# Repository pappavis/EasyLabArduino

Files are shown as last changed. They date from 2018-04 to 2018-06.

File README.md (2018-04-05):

### EasyLab Arduino Robotauto
Arduino Robot alles-op-één bordje door **Michiel Erasmus** / EasyLab4Kids. Dit is die tegniese ontwerpe daarvan.<br/>

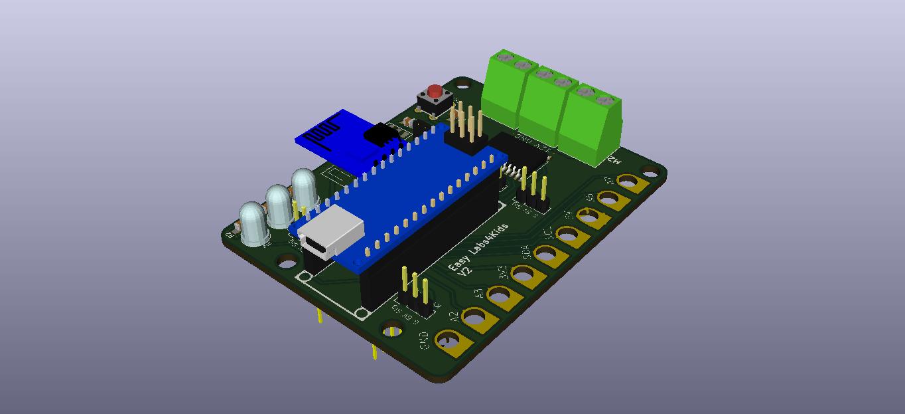
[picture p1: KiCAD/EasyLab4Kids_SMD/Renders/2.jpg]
<br/>

Credits:
---
**Ontwerp** deur Michiel Erasmus<br/>
**Kontak** thebapodcast@gmail.com<br/>
**Voorbeelde** https://www.facebook.com/EasyBlocks4Kids/<br/>
<br/>

EasyLab basis
---
Wat maak die EasyLab so besonder?<br/>
 - Robotauto op die planeet **MARS!!**
 - Volledig praktyk getest op kinders in Nederland<br/>
 - Beskikbaar met online lesmateriaal in Zuid-Afrikaans en Nederlands<br/>
 
EasyLab tegniese moontlikhede
---
Vir mense met 'n computer brein..<br/>
 - Support vir 2x robotmotors<br/>
 - 1x servo aansluiting<br/>
 - 2x Lynvolg snesore aansluitinge
 - 7x koperplaat aansluiting om maklik 'goedkope' aliexpress-sensore te kan gebruik<br/>
 - Skroefverbindinge vir robotmotors<br/>
 - GPIO en IO-poorte is almal beskikbaar
 - Beskikbaar in twee smake: Arduino en Raspberry Pi<br/>
 <br/>
 Elke EasyLab wordt ambagtelik in Den Haag, Nederland gemaak deur personeel met 'n mentaal of fysieke beperking. Dit help mee aan 'n menswaardig bestaan.<br/>

Self probeer?
---
kyk dan op https://www.facebook.com/EasyBlocks4Kids/ <br/>
<br/>
**EasyLab4Kids met LCD skerm en afstandmeting sensor;**<br/>
<br/>
<br/>
**EasyLab nuusgierige by CoderDojo Den Haag, Nederland [Jun-2017]**<br/>
<br/>
<br/>
Wil jy ook 'n EasyLab? Kontak thebapodcast@gmail.com<br/>
<br/>
<br/>
#easylab4kids #easyblocks4kids #arduinorobot
<br/>

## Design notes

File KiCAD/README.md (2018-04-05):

Arduino robot aansturing en breakout bordje<br/>
Ontwerp: Michiel Erasmus<br/>
<br/><br/>
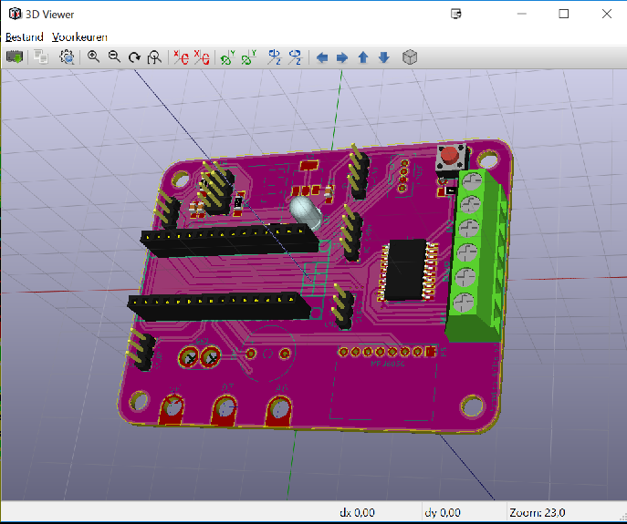
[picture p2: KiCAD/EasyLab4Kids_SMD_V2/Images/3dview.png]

<br/>

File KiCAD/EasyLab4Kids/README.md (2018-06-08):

###EasyLab Arduino V1.0
Arduino Nano versie.

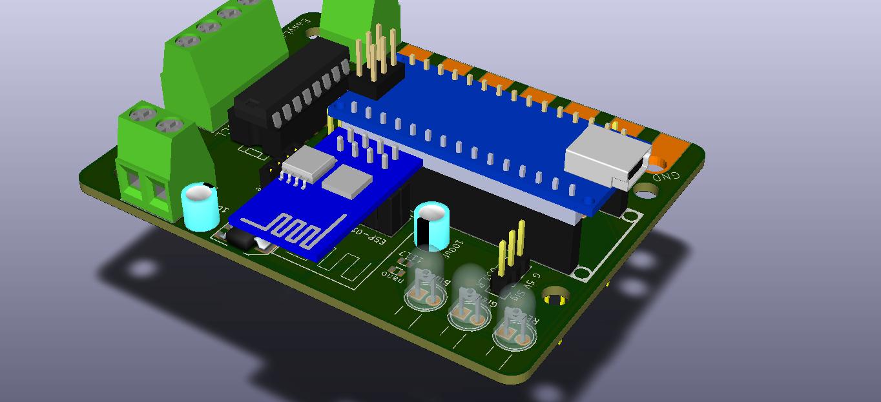
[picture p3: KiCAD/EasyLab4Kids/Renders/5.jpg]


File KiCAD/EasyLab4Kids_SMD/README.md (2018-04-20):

EasyLab SMD-versie<br/>

Credits:
---
Ontwerp door Michiel Erasmus<br/>

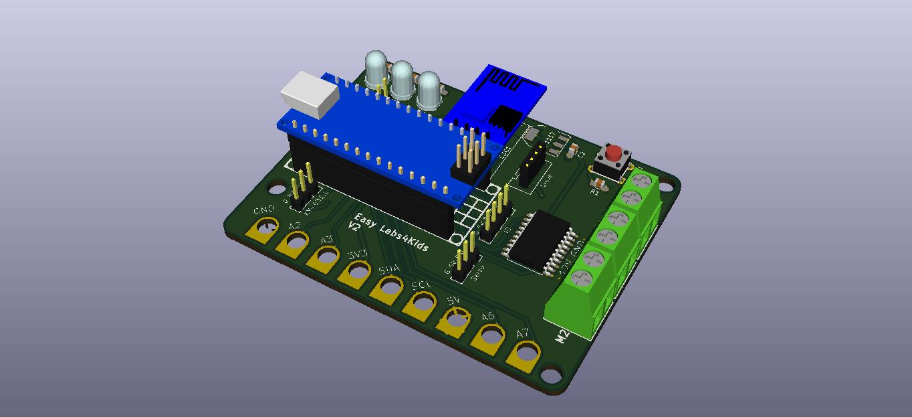
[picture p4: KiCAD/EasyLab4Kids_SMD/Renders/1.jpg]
<br/>

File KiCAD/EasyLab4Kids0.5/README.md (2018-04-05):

### EasyLab 0.5
prototype versie 0.5 ontwerp van **Michiel Erasmus**
<br/>

NIET GEBRUIKEN, dont use. Dit is 'n ou versie. <br/>
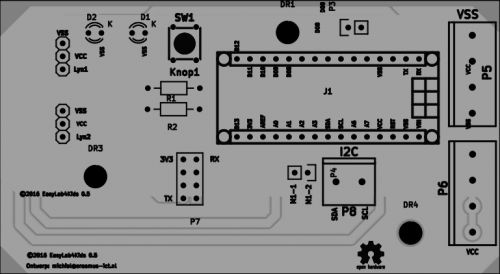
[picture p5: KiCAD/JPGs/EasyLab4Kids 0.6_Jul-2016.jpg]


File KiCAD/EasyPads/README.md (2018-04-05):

### EasyPads deur Michiel Erasmus
Makkelik sensore aansluit op Arduino en Raspberry Pi

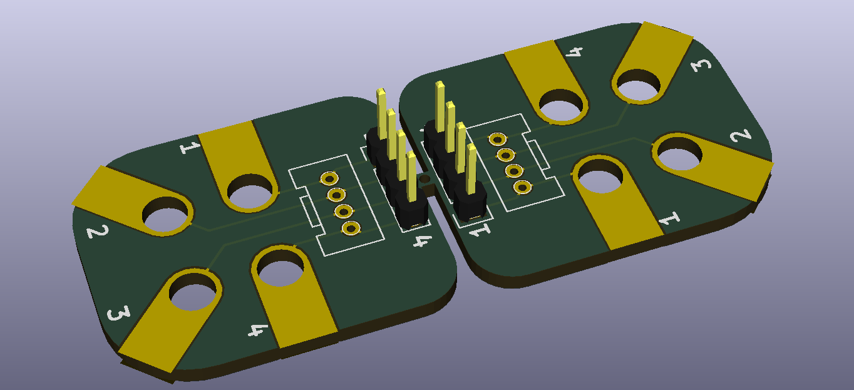
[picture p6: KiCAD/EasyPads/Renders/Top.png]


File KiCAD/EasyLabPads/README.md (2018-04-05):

### decprecated. NIET gebruik.
Dit projek het verval. Moet dit nie gebruik.<br/>

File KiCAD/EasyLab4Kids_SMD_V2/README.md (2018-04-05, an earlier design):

EasyLab V2  -- 13-01-2018
---
<br/>
Arduino robot uitbreidingsbord.<br/>
<br/>
Verbeterde  Arduino versie;<br/>
 - 6DOF sensor support<br/>
 - Onboard zoemer<br/>
 - Onboard L923D robot aansturing
 - Arduino nano
<br/>
**Credits:**<br/>
 - Layout -- Hemal Chevli @fiverr<br/>
 - Ontwerp en spesifikasies -- Michiel Erasmus<br/>
<br/>
<br/>

<br/>
EasyLab v2 met MPU-6050 sensor.


<br/>
Copyrights:<br/>
©2018 EasyLab4Kids en Michiel Erasmus
<br/>

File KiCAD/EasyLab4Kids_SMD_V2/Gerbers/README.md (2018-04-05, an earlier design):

GERBERs is stuur jy na 'n printplaat vervaardiger soos <a href="http://dirtyPCBs.com">dirtyPCBs</a><br/>
<br/>

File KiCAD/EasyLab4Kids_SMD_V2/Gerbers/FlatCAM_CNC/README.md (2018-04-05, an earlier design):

<a href="http://FlatCAM.org" target ="_blank">FlatCAM</a> is 'n programma waarmee jy GERBERs kan omsit na CNC-machine gcode.<br/>
<br/>
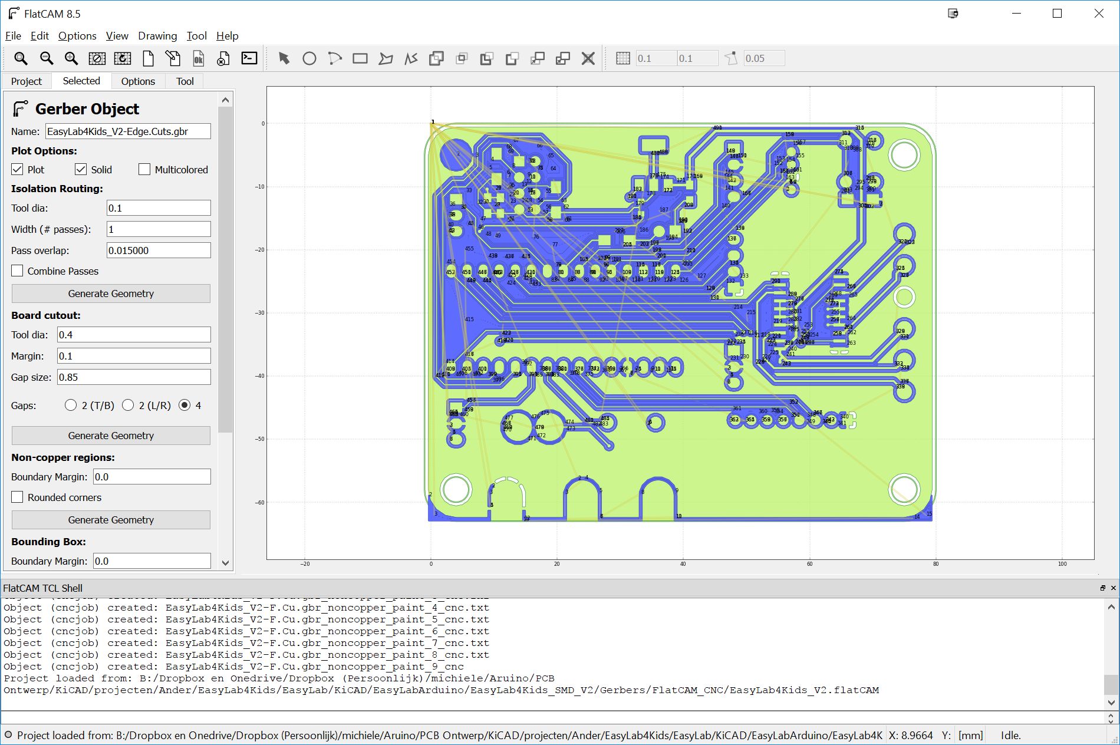
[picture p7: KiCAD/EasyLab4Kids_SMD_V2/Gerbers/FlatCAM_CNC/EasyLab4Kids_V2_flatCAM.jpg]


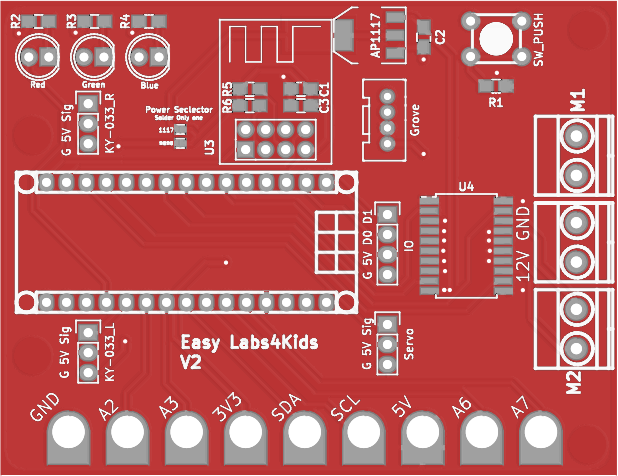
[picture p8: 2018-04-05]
KiCAD/EasyLab4Kids_SMD/Renders/EasyLab4Kids_SMD.png

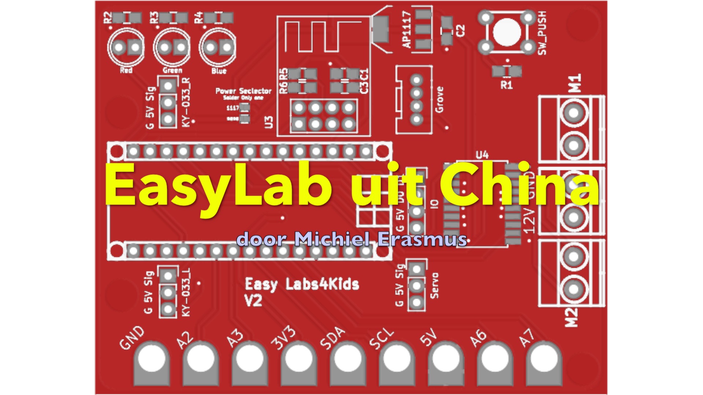
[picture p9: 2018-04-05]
KiCAD/EasyLab4Kids_SMD/Renders/EasyLab4Kids SMD-versie_plaatje.jpg

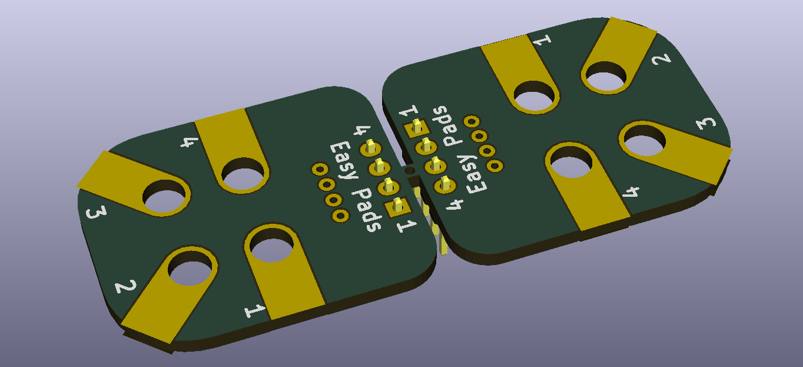
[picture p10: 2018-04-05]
KiCAD/EasyPads/Renders/Bottom.png

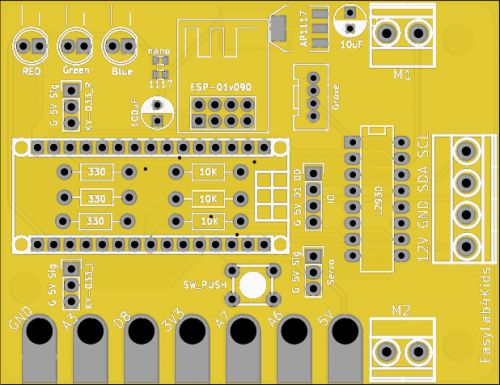
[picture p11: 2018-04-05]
KiCAD/JPGs/EasyLab4Kids 1.0_Jan-2017.jpg

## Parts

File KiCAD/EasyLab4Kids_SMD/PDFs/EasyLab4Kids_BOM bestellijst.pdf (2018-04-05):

EasyLab4Kids

Id | Designator | Package | Quantity | Designation
1 P11 | | mkds_1,5-2 | 1 M1
2 C1 | | C_0805_HandSoldering | 1100uF
3 C2 | | C_0805_HandSoldering | 110uF/16V
4 C3 | | C_0805_HandSoldering | 110uF
5 D1 | | LED-5MM | 1 Red
6 D2 | | LED-5MM | 1 Green
7 D3 | | LED-5MM | 1 Blue
8 J1 | | arduino_nano_header | 1 Arduino_Nano_Header
9 P8 | | Pin_Header_Straight_1x03 | 1 Servo
10 P9 | | Pin_Header_Straight_1x04 | 1IO
11 P10 | | grove_1x04 | 1 Grove
12 P12 | | mkds_1,5-2 | 1 M2
13 P13 | | mkds_1,5-2 | 1 PWR IN
14 R1,R5,R6 | | C_0805_HandSoldering | 310K
15 R2,R3,R4 | | C_0805_HandSoldering | 3330
16 SW1 | | PCB_PUSH_edit | 1 SW_PUSH
17 U1 | | Pin_Header_Straight_1x03 | 1 KY-033_L
18 U2 | | Pin_Header_Straight_1x03 | 1 KY-033_R
19 U5 | | SOT-223 | 1 AP1117
20 P1 | | BBC_CONNECTOR | 13.3V
21 P2 | | BBC_CONNECTOR | 15V
22 P3,P4,P16,P17 | | BBC_CONNECTOR | 4 D
23 P5,P6 | | BBC_CONNECTOR | 2 A
24 P7 | | BBC_CONNECTOR | 1 GND
25 P14,P15 | | SolderJumper | 2 SolderJumper
26 U3 | | ESP-01_SilkScreen | 1 ESP-01v090
27 U4 | | SOIC-20_7.5x12.8mm_Pitch1.27mm | 1L293D_SMD

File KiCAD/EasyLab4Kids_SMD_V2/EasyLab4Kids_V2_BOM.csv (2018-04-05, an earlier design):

Title | EasyLab4Kids_V2
Revision
Date | 2018-01-13
Generated | 13-1-2018 22:47:05
Company
Comment 1 | https://www.fiverr.com/users/hemalchevli/
Comment 2 | Drawn By: Hemal Chevli
Comment 3
Comment 4
Total Parts | 30
Total Unique Parts | 26
Ref | Qty | Value | Footprint
C2 C3 | 2 | C | EasyLabs4Kids:C_0805_HandSoldering
C1 | 1 | 10uF/16V | EasyLabs4Kids:C_0805_HandSoldering
D1 | 1 | LED | EasyLabs4Kids:LED-5MM
J1 | 1 | Arduino_Nano_Header | EasyLabs4Kids:arduino_nano_header
P1 | 1 | PWR | EasyLabs4Kids:mkds_1 | 5-2
P9 | 1 | A | EasyLabs4Kids:BBC_CONNECTOR
P10 | 1 | D | EasyLabs4Kids:BBC_CONNECTOR
P11 | 1 | 5V | EasyLabs4Kids:BBC_CONNECTOR
P15 | 1 | GND | EasyLabs4Kids:Makey_conn_3.2mm
P16 | 1 | SERVO | EasyLabs4Kids:Pin_Header_Straight_1x03
P14 | 1 | KY-038 | EasyLabs4Kids:Pin_Header_Straight_1x04
P12 | 1 | GROVE | EasyLabs4Kids:grove_1x04
P2 | 1 | KY-033_L | EasyLabs4Kids:Pin_Header_Straight_1x03
P3 | 1 | KY_033_R | EasyLabs4Kids:Pin_Header_Straight_1x03
P6 | 1 | MPU6050 | EasyLabs4Kids:MPU-6050
P8 P7 | 2 | SolderJumper | EasyLabs4Kids:SolderJumper
P4 | 1 | M1 | EasyLabs4Kids:mkds_1 | 5-2
P5 | 1 | M2 | EasyLabs4Kids:mkds_1 | 5-2
R1 | 1 | 330 | Resistors_SMD:R_1206_HandSoldering
R3 R4 R2 | 3 | R | Resistors_SMD:R_1206_HandSoldering
SP1 | 1 | Buzzer | EasyLabs4Kids:Buzzer_12x9.5RM7.6
SW1 | 1 | Button | EasyLabs4Kids:PCB_PUSH_edit
U4 | 1 | ESP-01v090 | EasyLabs4Kids:ESP-01_SilkScreen
U3 | 1 | HC-SR04 | EasyLabs4Kids:Pin_Header_Straight_1x04
U1 | 1 | L293D_SMD | EasyLabs4Kids:SOIC-20_7.5x12.8mm_Pitch1.27mm
U2 | 1 | AP1117 | TO_SOT_Packages_SMD:SOT-223
BOM made with KICAD_BOM_WIZARD (https://github.com/HashDefineElectronics/KiCad_BOM_Wizard.git)
Generated 13-1-2018 22:47:05

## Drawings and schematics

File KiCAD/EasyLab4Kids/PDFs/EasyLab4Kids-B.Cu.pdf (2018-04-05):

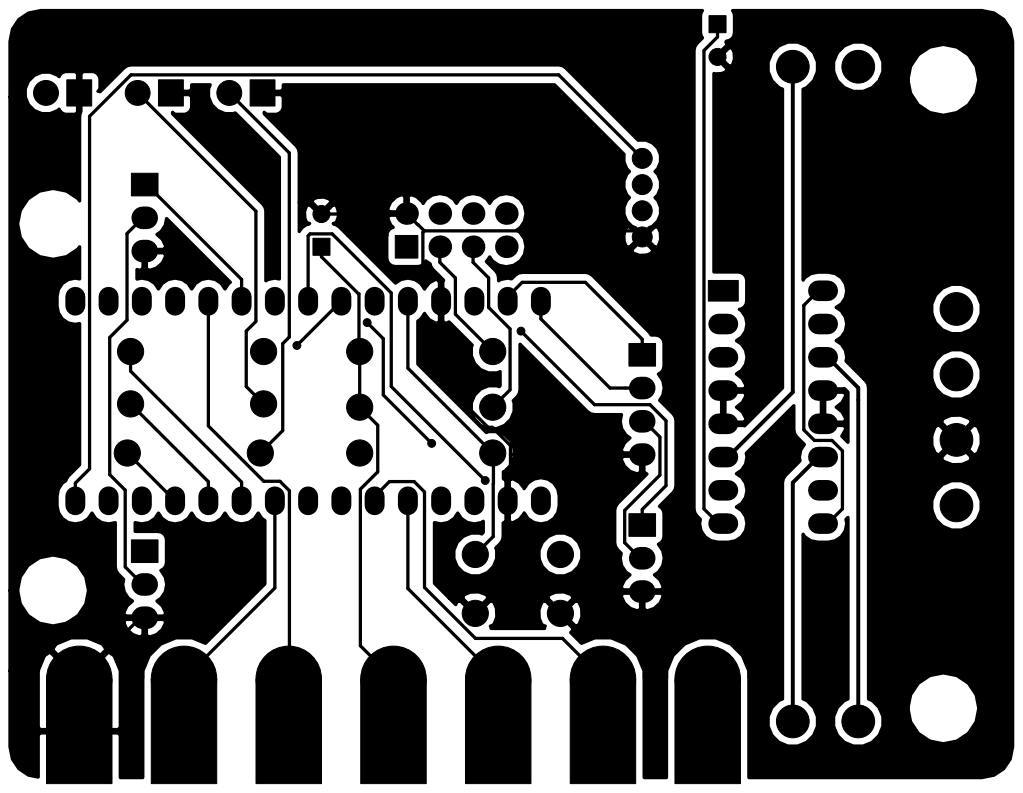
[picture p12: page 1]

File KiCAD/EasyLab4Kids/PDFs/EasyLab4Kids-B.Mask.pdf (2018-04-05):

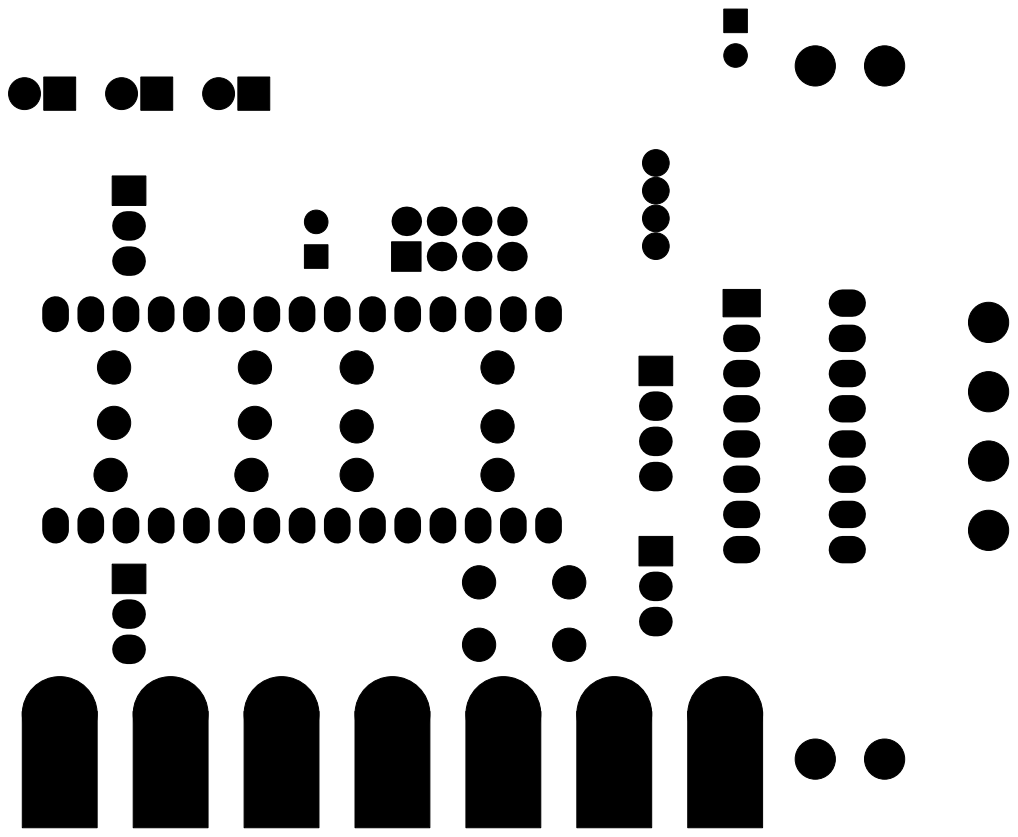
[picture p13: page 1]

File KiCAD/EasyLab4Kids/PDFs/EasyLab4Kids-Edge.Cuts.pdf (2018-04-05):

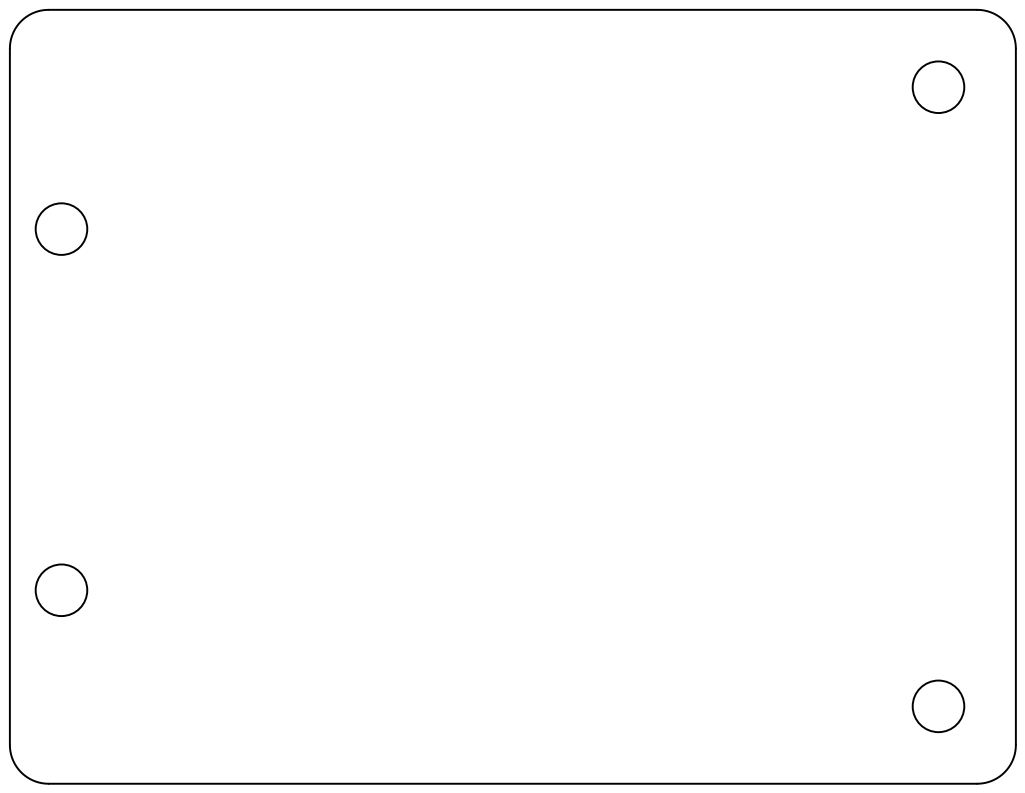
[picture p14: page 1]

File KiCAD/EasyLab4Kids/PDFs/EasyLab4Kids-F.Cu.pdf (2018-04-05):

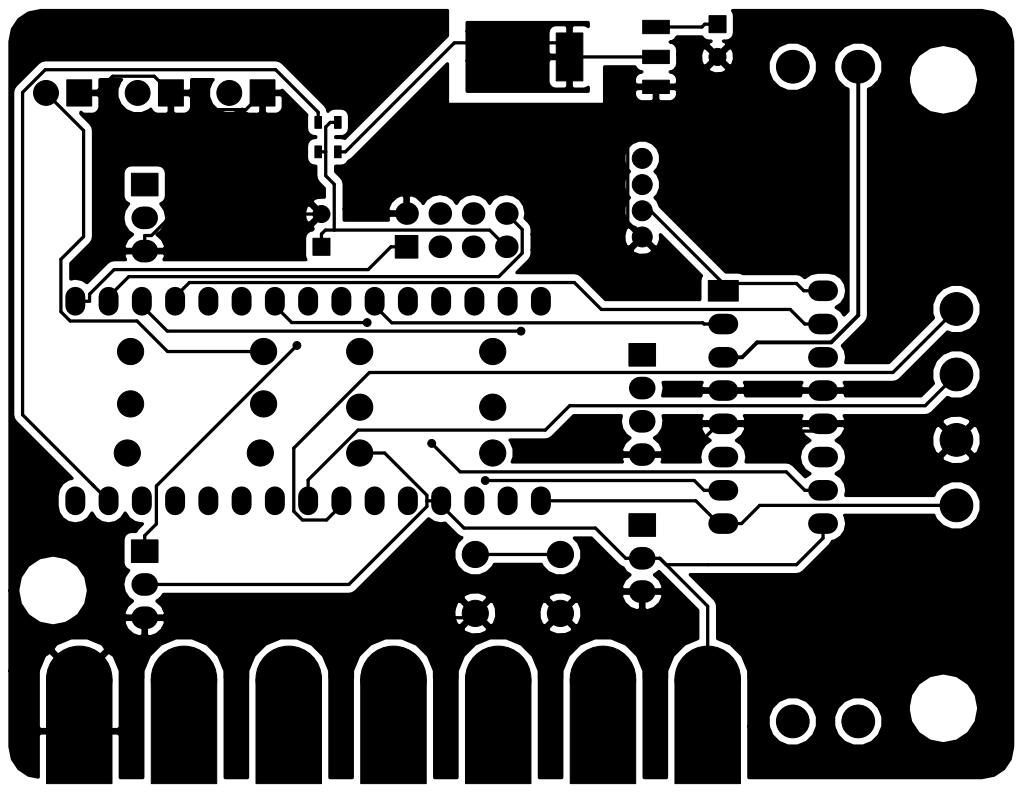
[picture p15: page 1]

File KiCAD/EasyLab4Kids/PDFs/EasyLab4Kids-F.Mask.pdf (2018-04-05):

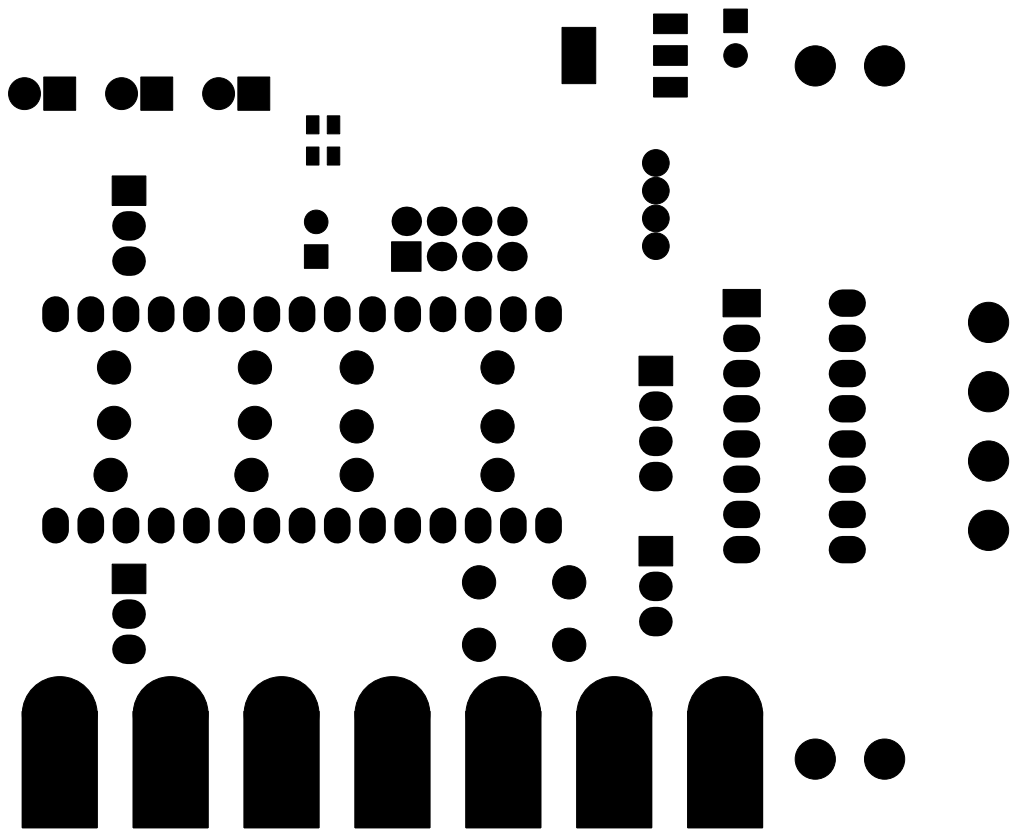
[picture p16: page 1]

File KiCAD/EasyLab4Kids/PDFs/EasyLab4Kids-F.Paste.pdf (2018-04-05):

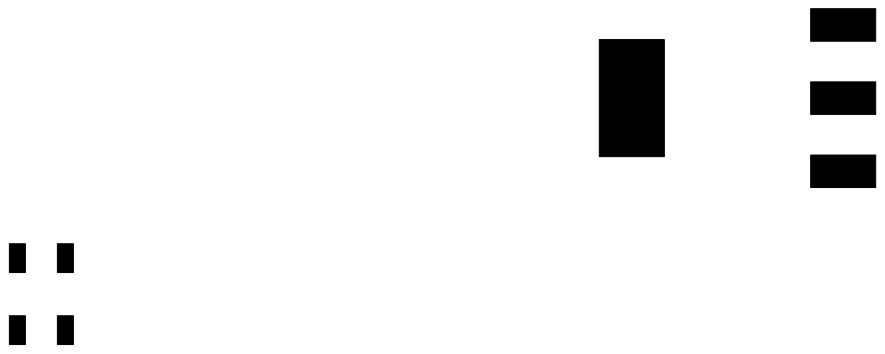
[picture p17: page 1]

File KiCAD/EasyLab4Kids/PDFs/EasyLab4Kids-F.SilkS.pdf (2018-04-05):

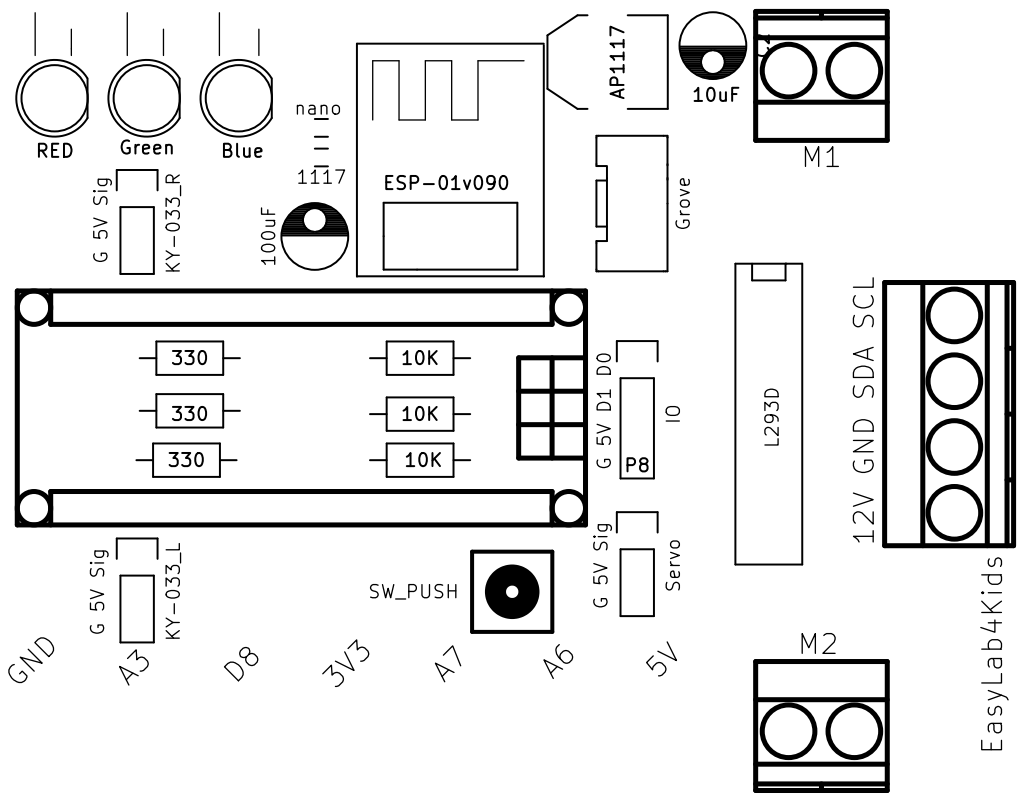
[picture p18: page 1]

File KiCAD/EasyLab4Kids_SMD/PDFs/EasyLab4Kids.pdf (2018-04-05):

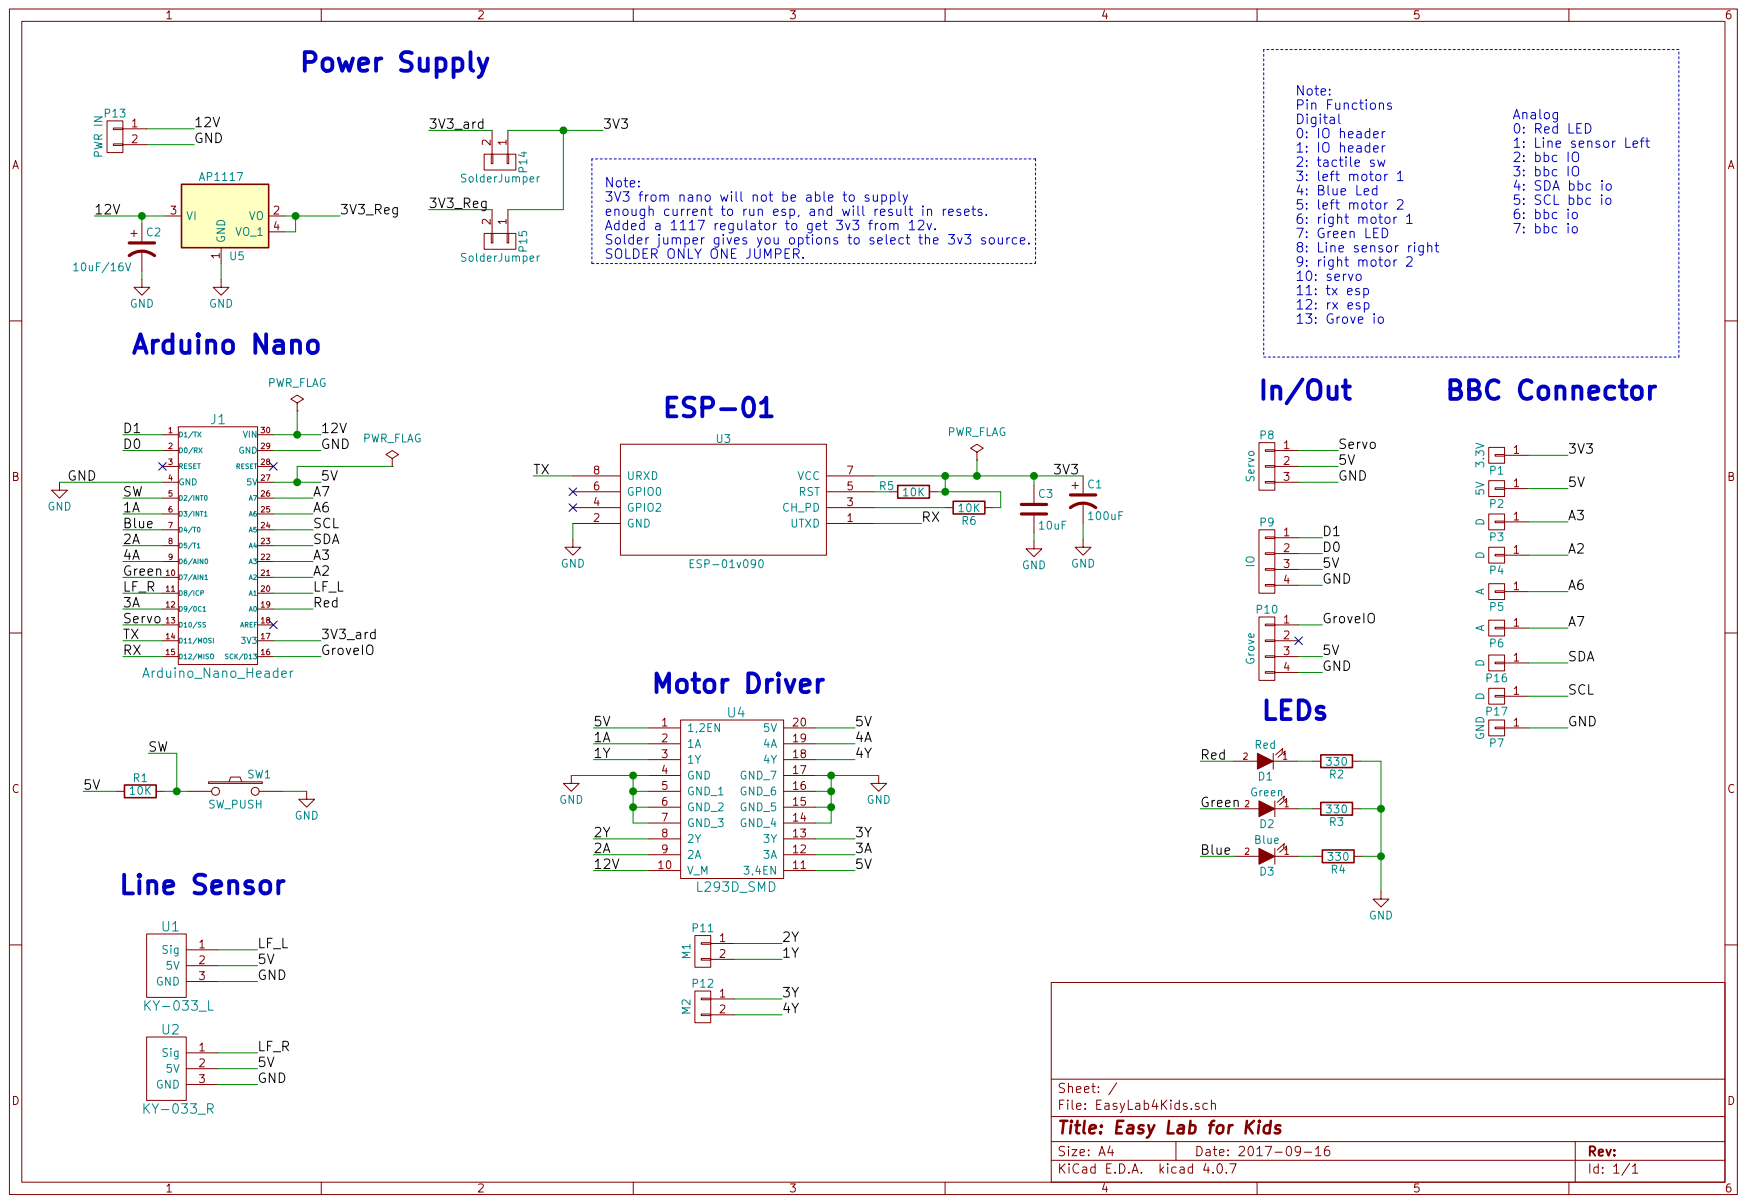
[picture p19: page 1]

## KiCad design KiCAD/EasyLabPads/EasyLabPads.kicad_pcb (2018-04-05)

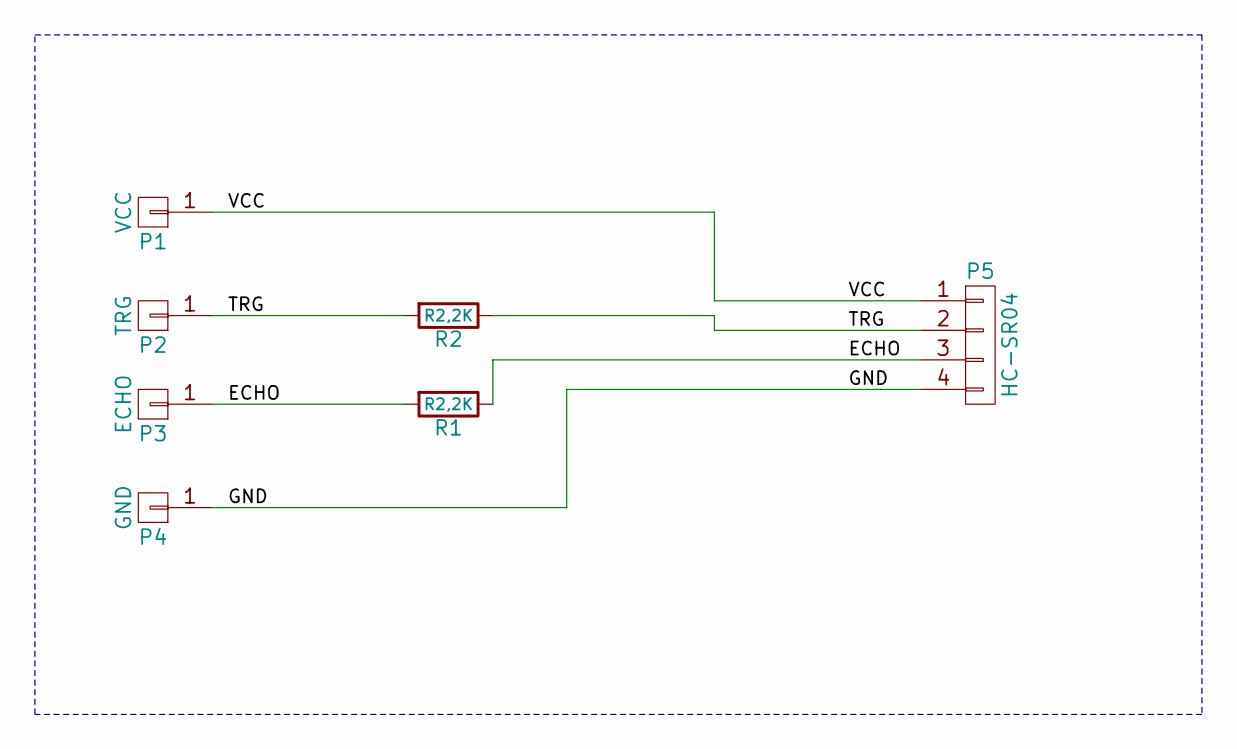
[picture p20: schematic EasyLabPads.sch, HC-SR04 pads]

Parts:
P1: VCC; z_BBC-BIT
P2: TRG; z_BBC-BIT
P3: ECHO; z_BBC-BIT
P4: GND; z_BBC-BIT
P5: HC-SR04; Pin_Header_Angled_1x04
R1, R2: R2,2K; Resistor_Vertical_RM5mm

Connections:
/ECHO: P3.1, P5.3, R1.1, R1.2
/GND: P4.1, P5.4
/TRG: P2.1, P5.2, R2.1, R2.2
/VCC: P1.1, P5.1

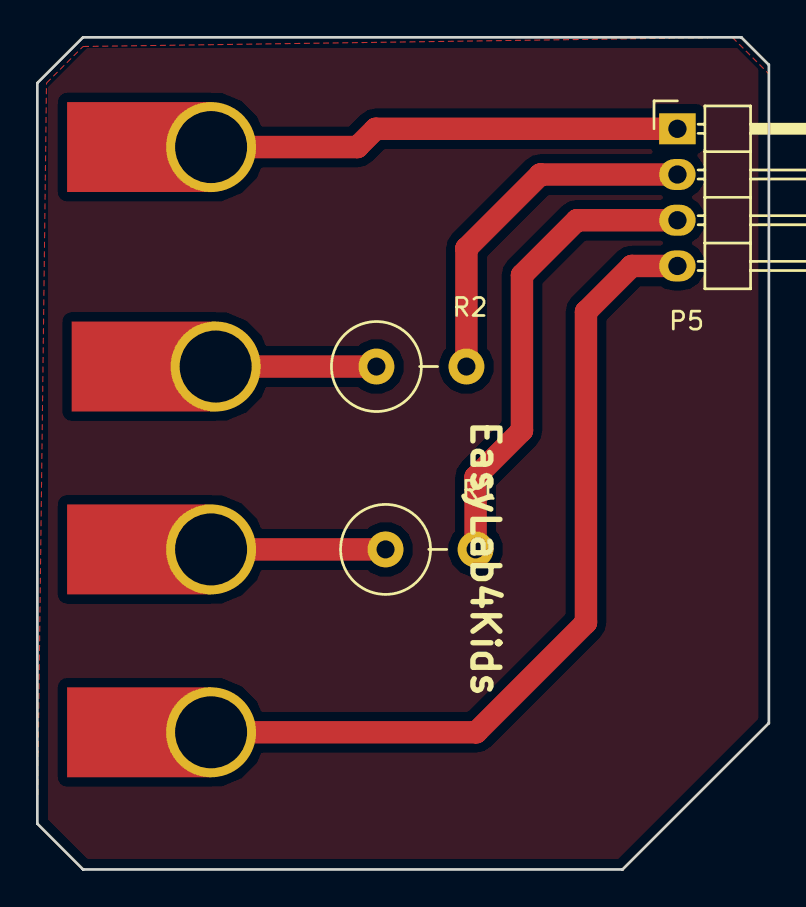
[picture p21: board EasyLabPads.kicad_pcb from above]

Board: 2 copper layers, 40.6 x 46.2 mm, 7 parts (0 on the bottom side), 4 nets.

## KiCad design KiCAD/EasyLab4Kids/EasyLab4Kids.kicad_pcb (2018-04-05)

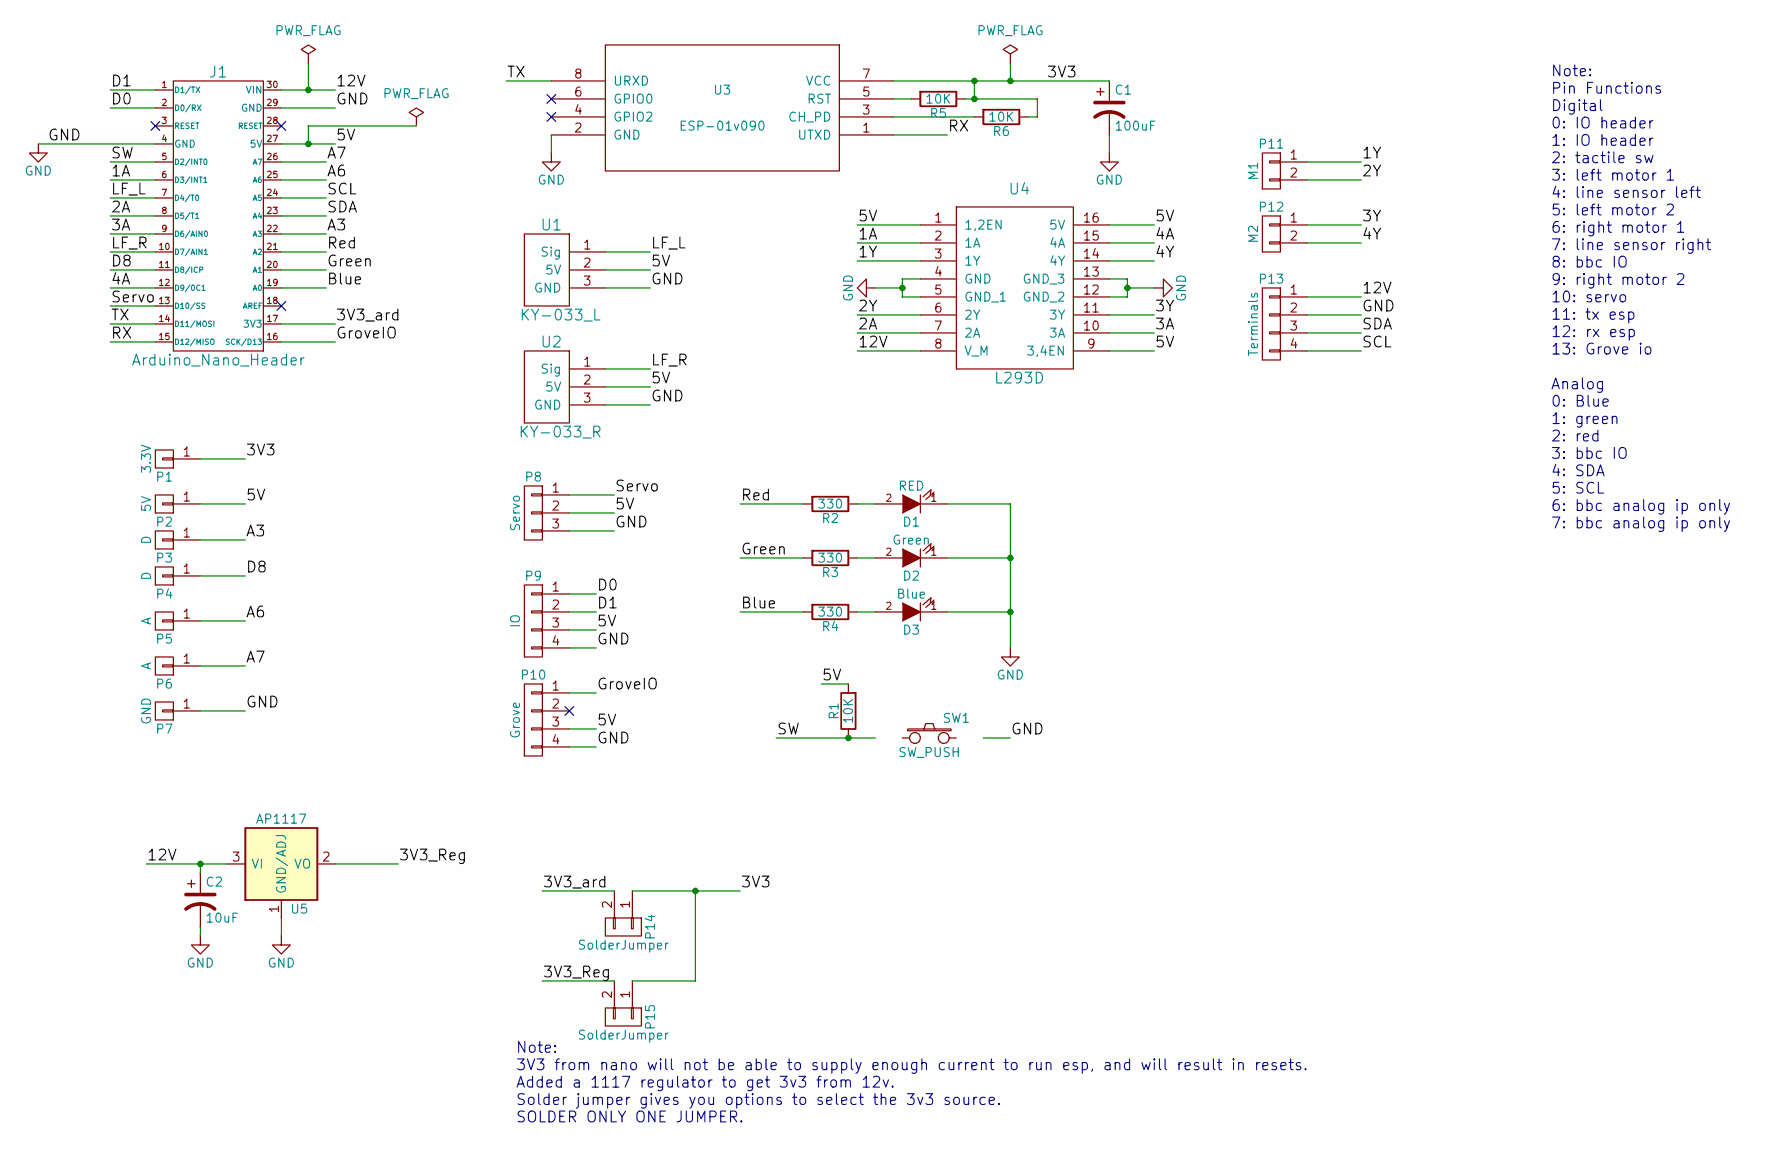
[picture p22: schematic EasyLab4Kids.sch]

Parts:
C1: 100uF; C_Radial_D5_L6_P2.5
C2: 10uF; C_Radial_D5_L6_P2.5
D1: RED; LED-5MM
D2: Green; LED-5MM
D3: Blue; LED-5MM
J1: Arduino_Nano_Header; arduino_nano_header
P1: 3.3V; z_BBC-BIT
P2: 5V; z_BBC-BIT
P3, P4: D; z_BBC-BIT
P5, P6: A; z_BBC-BIT
P7: GND; z_BBC-BIT
P8: Servo; Pin_Header_Straight_1x03
P9: IO; Pin_Header_Straight_1x04
P10: Grove; grove_1x04
P11: M1; mkds_1,5-2
P12: M2; mkds_1,5-2
P13: Terminals; mkds_1,5-4
P14, P15: SolderJumper; R_0603
R1, R5, R6: 10K; Resistor_Horizontal_RM10mm
R2, R3, R4: 330; Resistor_Horizontal_RM10mm
SW1: SW_PUSH; PCB_PUSH_edit
U1: KY-033_L; Pin_Header_Straight_1x03
U2: KY-033_R; Pin_Header_Straight_1x03
U3: ESP-01v090; ESP-01_SilkScreen
U4: L293D; DIP-16__300_ELL
U5: AP1117; SOT-223

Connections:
/1A: J1.6 (D3/INT1), U4.2 (1A)
/1Y: P11.1, U4.3 (1Y)
/2A: J1.8 (D5/T1), U4.7 (2A)
/2Y: P11.2, U4.6 (2Y)
/3A: J1.9 (D6/AIN0), U4.10 (3A)
/3V3: C1.1, P1.1, P14.1, P15.1, R5.1, R6.1, U3.7 (VCC)
/3V3_Reg: P15.2, U5.2 (VO), U5.4 (VO)
/3V3_ard: J1.17 (3V3), P14.2
/3Y: P12.1, U4.11 (3Y)
/4A: J1.12 (D9/0C1), U4.15 (4A)
/4Y: P12.2, U4.14 (4Y)
/5V: J1.27 (5V), P2.1, P8.2, P9.3, P10.3, R1.2, U1.2 (5V), U2.2 (5V), U4.1 (1,2EN), U4.9 (3,4EN), U4.16 (5V)
/12V: C2.1, J1.30 (VIN), P13.1, U4.8 (V_M), U5.3 (VI)
/A3: J1.22 (A3), P3.1
/A6: J1.25 (A6), P5.1
/A7: J1.26 (A7), P6.1
/Blue: J1.19 (A0), R4.2
/D0: J1.2 (D0/RX), P9.1
/D1: J1.1 (D1/TX), P9.2
/D8: J1.11 (D8/ICP), P4.1
/Green: J1.20 (A1), R3.2
/GroveIO: J1.16 (SCK/D13), P10.1
/LF_L: J1.7 (D4/T0), U1.1 (Sig)
/LF_R: J1.10 (D7/AIN1), U2.1 (Sig)
/RX: J1.15 (D12/MISO), U3.1 (UTXD)
/Red: J1.21 (A2), R2.2
/SCL: J1.24 (A5), P13.4
/SDA: J1.23 (A4), P13.3
/SW: J1.5 (D2/INT0), R1.1, SW1.1
/Servo: J1.13 (D10/SS), P8.1
/TX: J1.14 (D11/MOSI), U3.8 (URXD)
GND: C1.2, C2.2, D1.1 (K), D2.1 (K), D3.1 (K), J1.4 (GND), J1.29 (GND), P7.1, P8.3, P9.4, P10.4, P13.2, SW1.2, U1.3 (GND), U2.3 (GND), U3.2 (GND), U4.4 (GND), U4.5 (GND_1), U4.12 (GND_2), U4.13 (GND_3), U5.1 (GND/ADJ)
unnamed: D1.2 (A), R2.1
unnamed: D2.2 (A), R3.1
unnamed: D3.2 (A), R4.1
unnamed: R5.2, U3.5 (RST)
unnamed: R6.2, U3.3 (CH_PD)

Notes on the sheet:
Note: Pin Functions Digital 0: IO header 1: IO header 2: tactile sw 3: left motor 1 4: line sensor left 5: left motor 2 6: right motor 1 7: line sensor right 8: bbc IO 9: right motor 2 10: servo 11: tx esp 12: rx esp 13: Grove io Analog 0: Blue 1: green 2: red 3: bbc IO 4: SDA 5: SCL 6: bbc analog 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
Note: 3V3 from nano will not be able to supply enough current to run esp, and will result in resets. Added a 1117 regulator to get 3v3 from 12v. Solder jumper gives you options to select the 3v3 source. SOLDER ONLY ONE JUMPER.

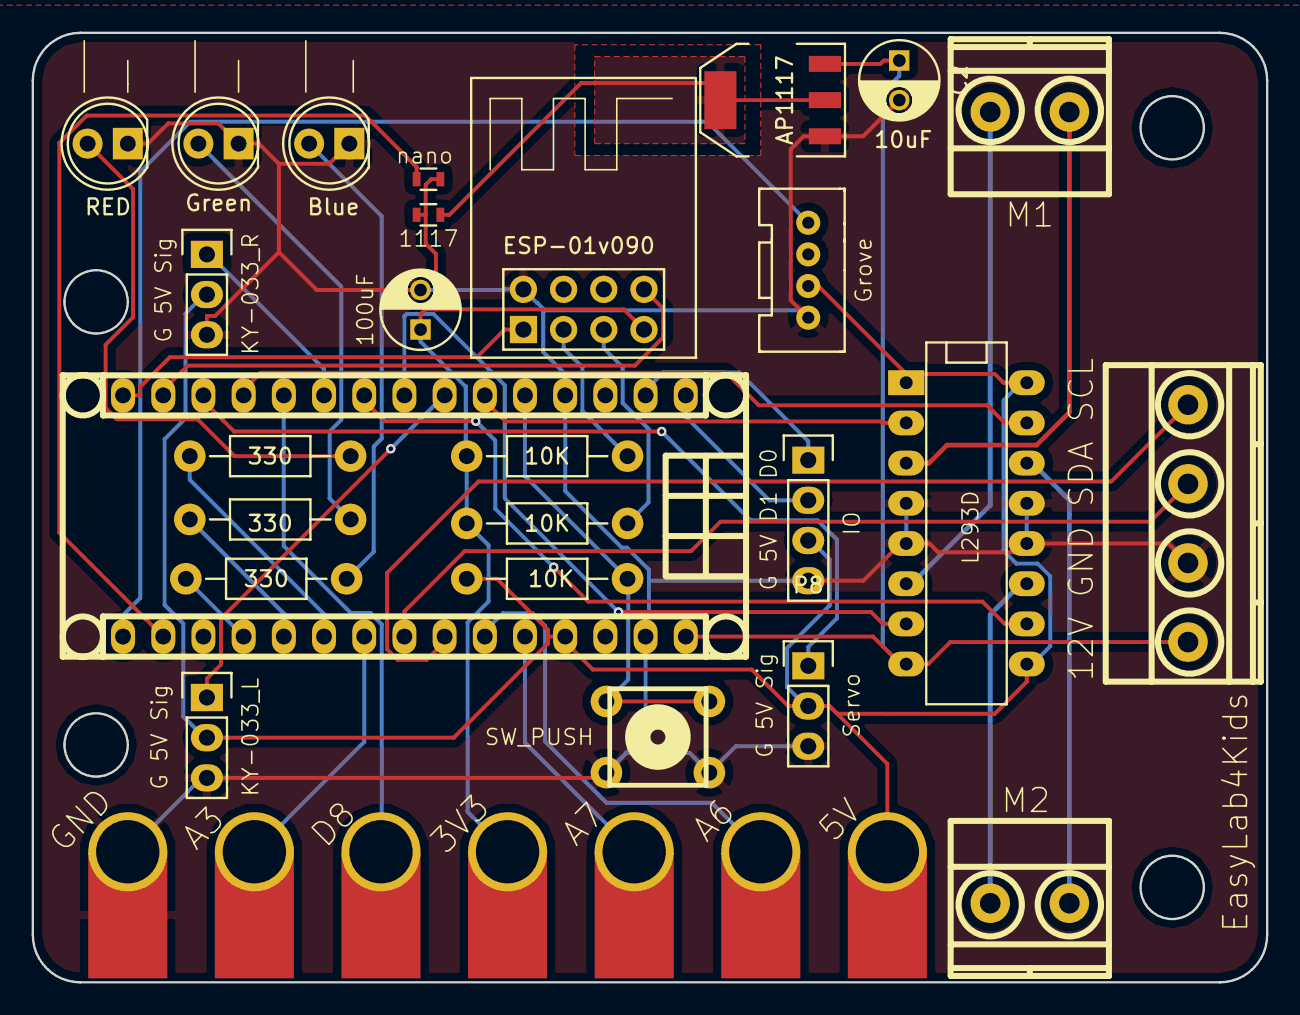
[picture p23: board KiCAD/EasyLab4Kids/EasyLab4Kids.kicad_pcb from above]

Board: 2 copper layers, 78.0 x 60.0 mm, 33 parts (0 on the bottom side), 37 nets.

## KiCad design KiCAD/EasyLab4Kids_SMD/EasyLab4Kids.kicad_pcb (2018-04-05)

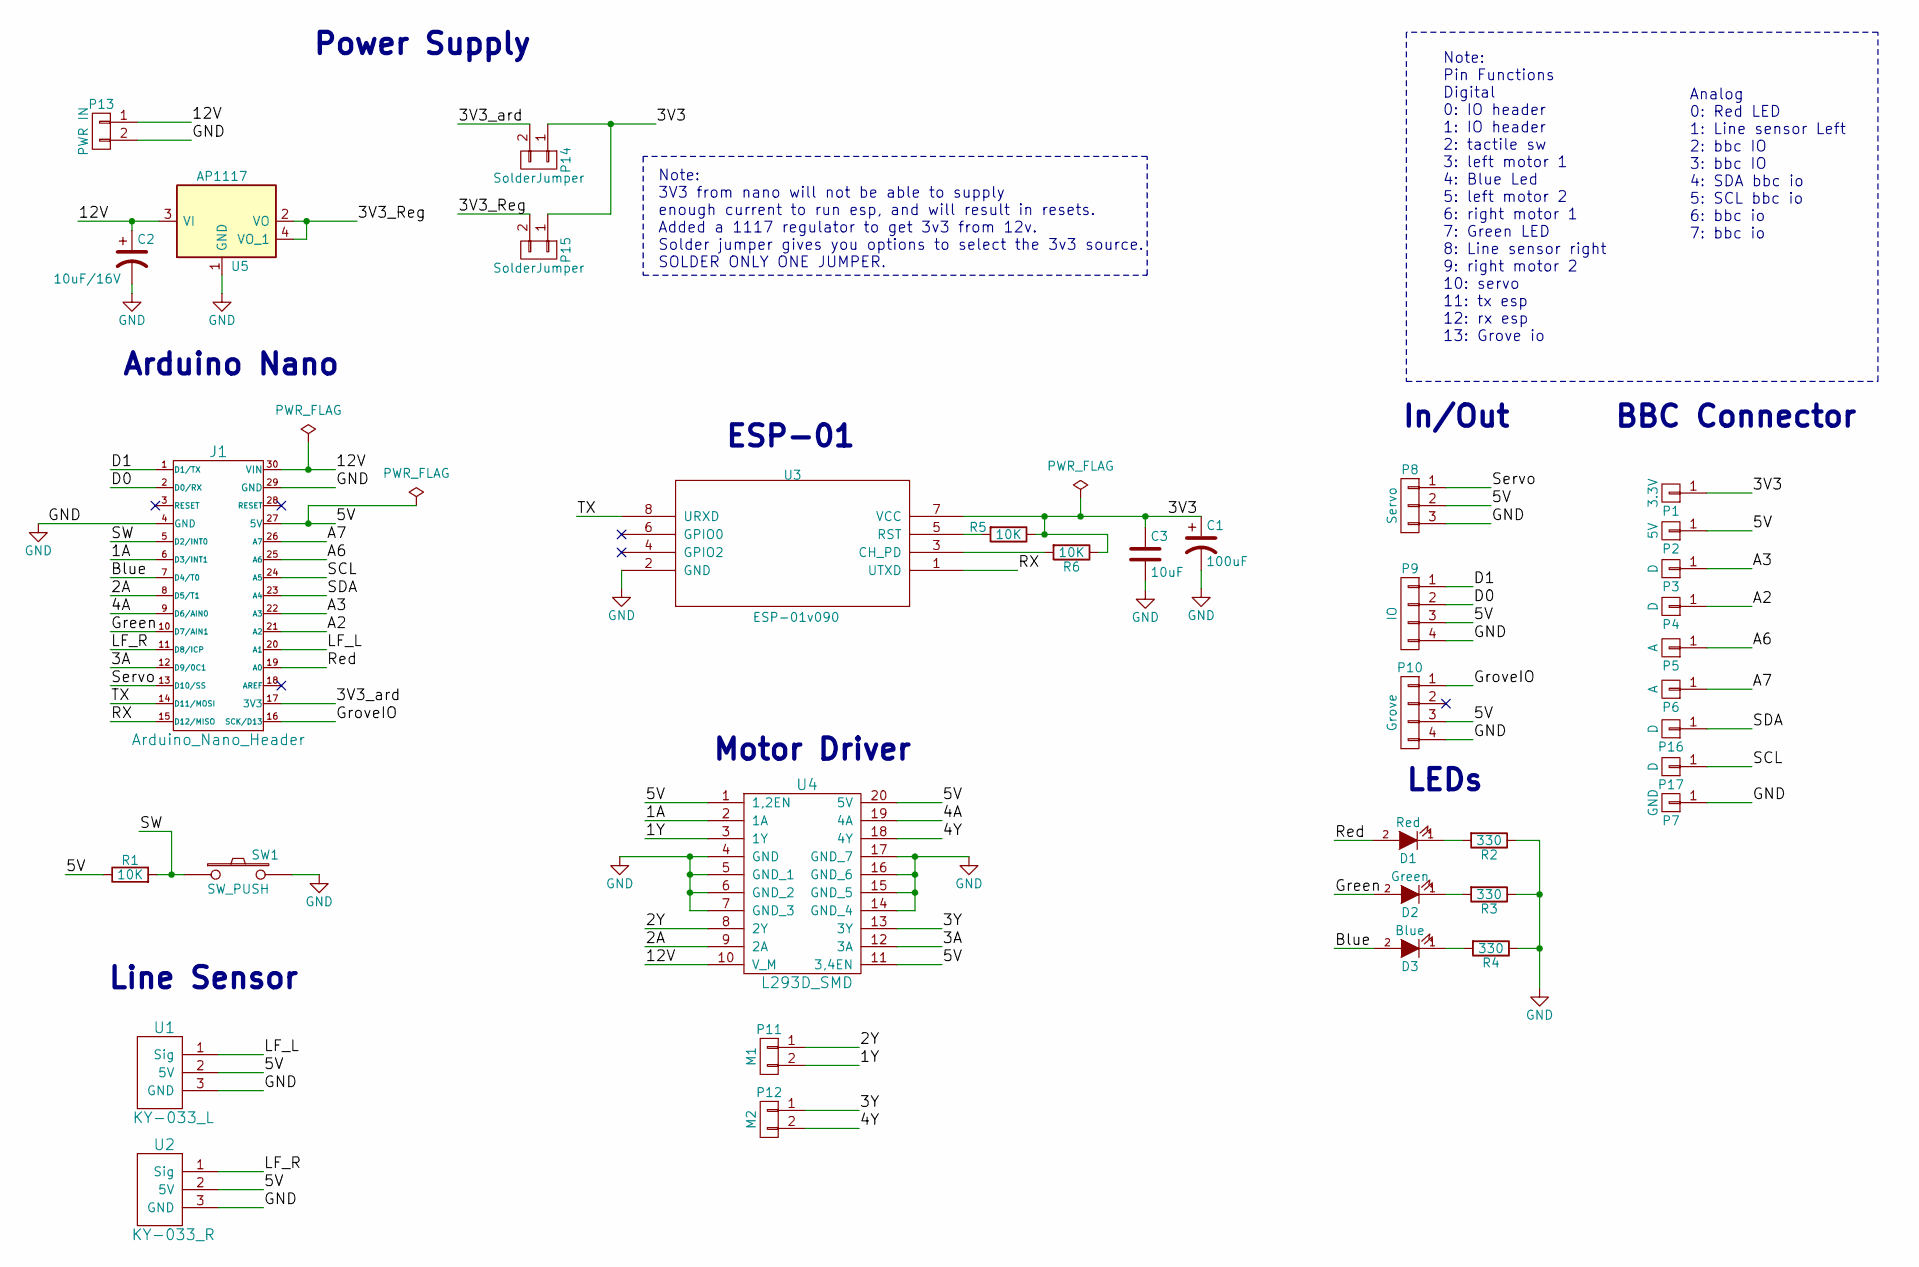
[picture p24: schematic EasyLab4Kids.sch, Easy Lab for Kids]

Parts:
C1: 100uF; C_0805_HandSoldering
C2: 10uF/16V; C_0805_HandSoldering
C3: 10uF; C_0805_HandSoldering
D1: Red; LED-5MM
D2: Green; LED-5MM
D3: Blue; LED-5MM
J1: Arduino_Nano_Header; arduino_nano_header
P1: 3.3V; BBC_CONNECTOR
P2: 5V; BBC_CONNECTOR
P3, P4, P16, P17: D; BBC_CONNECTOR
P5, P6: A; BBC_CONNECTOR
P7: GND; BBC_CONNECTOR
P8: Servo; Pin_Header_Straight_1x03
P9: IO; Pin_Header_Straight_1x04
P10: Grove; grove_1x04
P11: M1; mkds_1,5-2
P12: M2; mkds_1,5-2
P13: PWR IN; mkds_1,5-2
P14, P15: SolderJumper
R1, R5, R6: 10K; C_0805_HandSoldering
R2, R3, R4: 330; C_0805_HandSoldering
SW1: SW_PUSH; PCB_PUSH_edit
U1: KY-033_L; Pin_Header_Straight_1x03
U2: KY-033_R; Pin_Header_Straight_1x03
U3: ESP-01v090; ESP-01_SilkScreen
U4: L293D_SMD; SOIC-20_7.5x12.8mm_Pitch1.27mm
U5: AP1117; SOT-223

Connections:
/1A: J1.6 (D3/INT1), U4.2 (1A)
/1Y: P11.2, U4.3 (1Y)
/2A: J1.8 (D5/T1), U4.9 (2A)
/2Y: P11.1, U4.8 (2Y)
/3A: J1.12 (D9/0C1), U4.12 (3A)
/3V3: C1.1, C3.1, P1.1, P14.1, P15.1, R5.1, R6.1, U3.7 (VCC)
/3V3_Reg: P15.2, U5.2 (VO), U5.4 (VO_1)
/3V3_ard: J1.17 (3V3), P14.2
/3Y: P12.1, U4.13 (3Y)
/4A: J1.9 (D6/AIN0), U4.19 (4A)
/4Y: P12.2, U4.18 (4Y)
/5V: J1.27 (5V), P2.1, P8.2, P9.3, P10.3, R1.1, U1.2 (5V), U2.2 (5V), U4.1 (1,2EN), U4.11 (3,4EN), U4.20 (5V)
/12V: C2.1, J1.30 (VIN), P13.1, U4.10 (V_M), U5.3 (VI)
/A2: J1.21 (A2), P4.1
/A3: J1.22 (A3), P3.1
/A6: J1.25 (A6), P5.1
/A7: J1.26 (A7), P6.1
/Blue: D3.2 (A), J1.7 (D4/T0)
/D0: J1.2 (D0/RX), P9.2
/D1: J1.1 (D1/TX), P9.1
/Green: D2.2 (A), J1.10 (D7/AIN1)
/GroveIO: J1.16 (SCK/D13), P10.1
/LF_L: J1.20 (A1), U1.1 (Sig)
/LF_R: J1.11 (D8/ICP), U2.1 (Sig)
/RX: J1.15 (D12/MISO), U3.1 (UTXD)
/Red: D1.2 (A), J1.19 (A0)
/SCL: J1.24 (A5), P17.1
/SDA: J1.23 (A4), P16.1
/SW: J1.5 (D2/INT0), R1.2, SW1.1
/Servo: J1.13 (D10/SS), P8.1
/TX: J1.14 (D11/MOSI), U3.8 (URXD)
GND: C1.2, C2.2, C3.2, J1.4 (GND), J1.29 (GND), P7.1, P8.3, P9.4, P10.4, P13.2, R2.1, R3.1, R4.1, SW1.2, U1.3 (GND), U2.3 (GND), U3.2 (GND), U4.4 (GND), U4.5 (GND_1), U4.6 (GND_2), U4.7 (GND_3), U4.14 (GND_4), U4.15 (GND_5), U4.16 (GND_6), U4.17 (GND_7), U5.1 (GND)
unnamed: D1.1 (K), R2.2
unnamed: D2.1 (K), R3.2
unnamed: D3.1 (K), R4.2
unnamed: R5.2, U3.5 (RST)
unnamed: R6.2, U3.3 (CH_PD)

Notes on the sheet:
Note: Pin Functions Digital 0: IO header 1: IO header 2: tactile sw 3: left motor 1 4: Blue Led 5: left motor 2 6: right motor 1 7: Green LED 8: Line sensor right 9: right motor 2 10: servo 11: tx esp 12: rx esp 13: Grove io
Note: 3V3 from nano will not be able to supply enough current to run esp, and will result in resets. Added a 1117 regulator to get 3v3 from 12v. Solder jumper gives you options to select the 3v3 source. SOLDER ONLY ONE JUMPER.
Power Supply
Arduino Nano
ESP-01
Line Sensor
Motor Driver
BBC Connector
In/Out
Analog 0: Red LED 1: Line sensor Left 2: bbc IO 3: bbc IO 4: SDA bbc io 5: SCL bbc io 6: bbc io 7: bbc io
LEDs

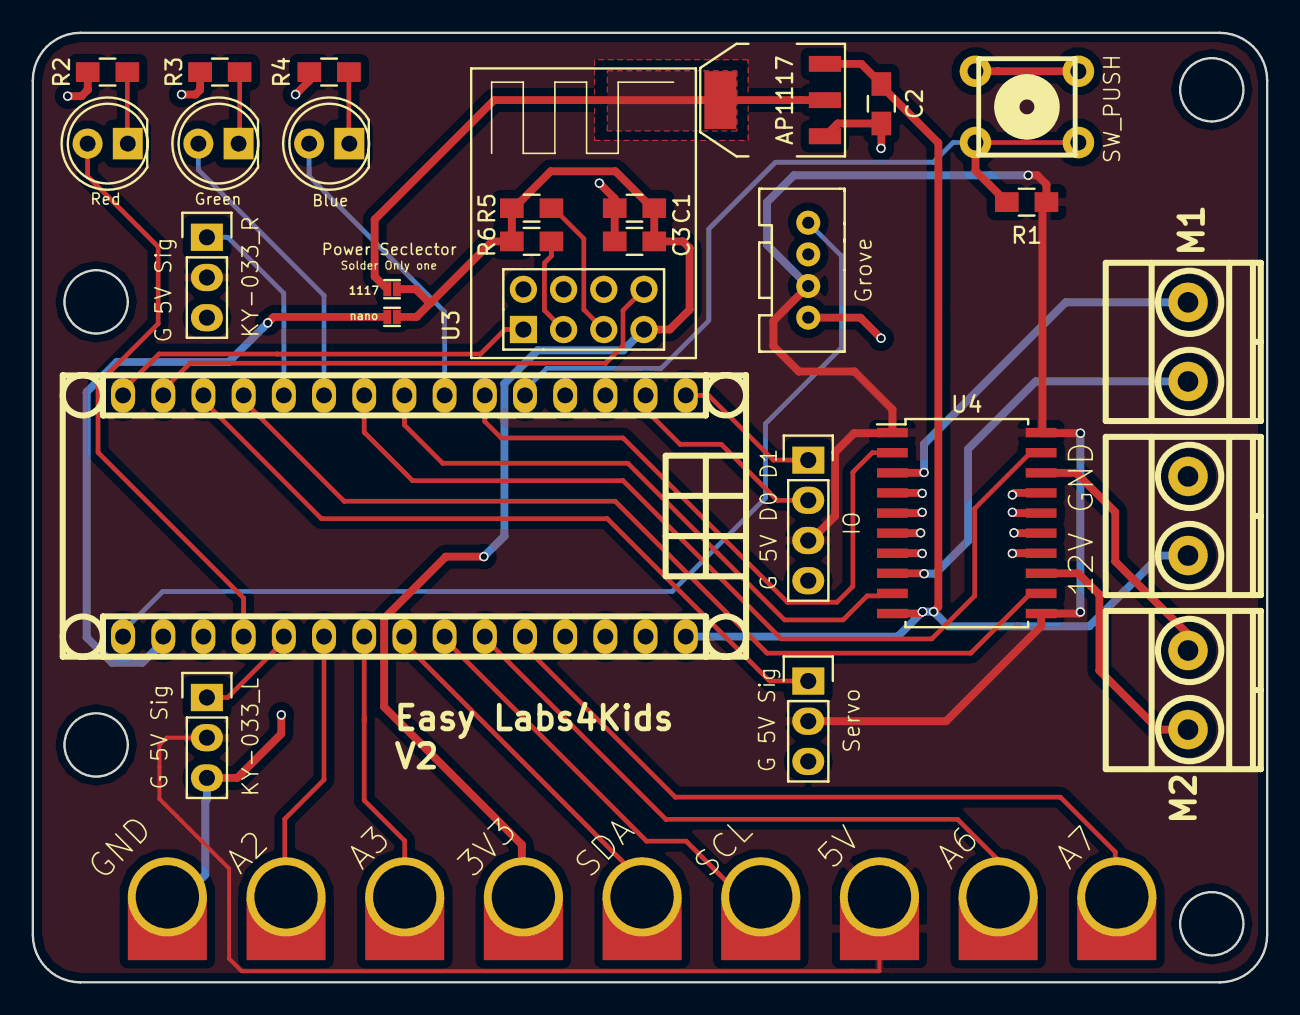
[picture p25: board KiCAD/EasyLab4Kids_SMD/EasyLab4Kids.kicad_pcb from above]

Board: 2 copper layers, 78.0 x 60.0 mm, 36 parts (0 on the bottom side), 37 nets.

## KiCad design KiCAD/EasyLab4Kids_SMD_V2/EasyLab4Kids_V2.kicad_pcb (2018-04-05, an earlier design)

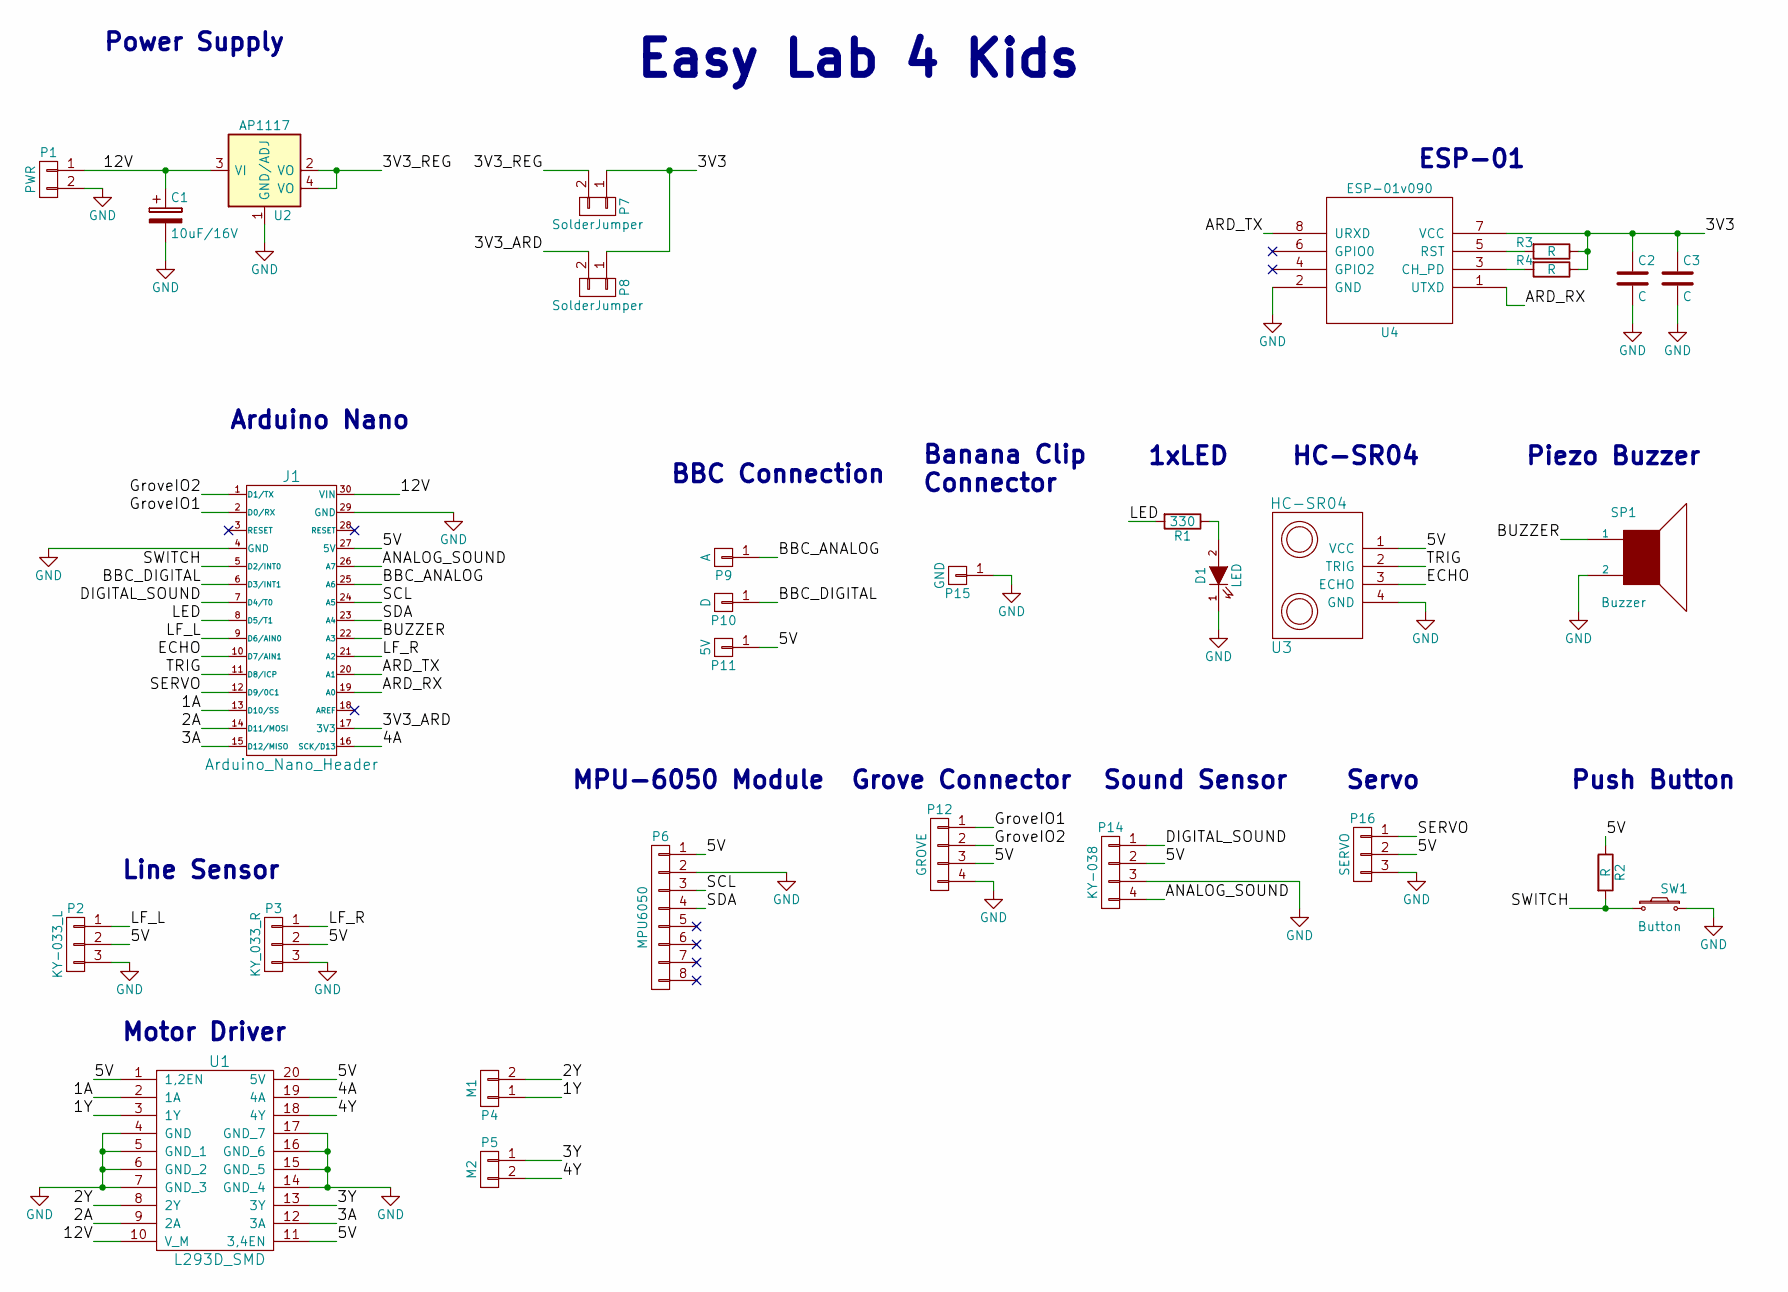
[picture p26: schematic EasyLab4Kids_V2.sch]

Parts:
C1: 10uF/16V; C_0805_HandSoldering
C2, C3: C; C_0805_HandSoldering
D1: LED; LED-5MM
J1: Arduino_Nano_Header; arduino_nano_header
P1: PWR; mkds_1,5-2
P2: KY-033_L; Pin_Header_Straight_1x03
P3: KY_033_R; Pin_Header_Straight_1x03
P4: M1; mkds_1,5-2
P5: M2; mkds_1,5-2
P6: MPU6050; MPU-6050
P7, P8: SolderJumper
P9: A; BBC_CONNECTOR
P10: D; BBC_CONNECTOR
P11: 5V; BBC_CONNECTOR
P12: GROVE; grove_1x04
P14: KY-038; Pin_Header_Straight_1x04
P15: GND; Makey_conn_3.2mm
P16: SERVO; Pin_Header_Straight_1x03
R1: 330; R_1206_HandSoldering
R2, R3, R4: R; R_1206_HandSoldering
SP1: Buzzer; Buzzer_12x9.5RM7.6
SW1: Button; PCB_PUSH_edit
U1: L293D_SMD; SOIC-20_7.5x12.8mm_Pitch1.27mm
U2: AP1117; SOT-223
U3: HC-SR04; Pin_Header_Straight_1x04
U4: ESP-01v090; ESP-01_SilkScreen

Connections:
/1A: J1.13 (D10/SS), U1.2 (1A)
/1Y: P4.1, U1.3 (1Y)
/2A: J1.14 (D11/MOSI), U1.9 (2A)
/2Y: P4.2, U1.8 (2Y)
/3A: J1.15 (D12/MISO), U1.12 (3A)
/3V3: C2.1, C3.1, P7.1, P8.1, R3.1, R4.1, U4.7 (VCC)
/3V3_ARD: J1.17 (3V3), P8.2
/3V3_REG: P7.2, U2.2 (VO), U2.4 (VO)
/3Y: P5.1, U1.13 (3Y)
/4A: J1.16 (SCK/D13), U1.19 (4A)
/4Y: P5.2, U1.18 (4Y)
/5V: J1.27 (5V), P2.2, P3.2, P6.1, P11.1, P12.3, P14.2, P16.2, R2.1, U1.1 (1,2EN), U1.11 (3,4EN), U1.20 (5V), U3.1 (VCC)
/12V: C1.1, J1.30 (VIN), P1.1, U1.10 (V_M), U2.3 (VI)
/ANALOG_SOUND: J1.26 (A7), P14.4
/ARD_RX: J1.19 (A0), U4.1 (UTXD)
/ARD_TX: J1.20 (A1), U4.8 (URXD)
/BBC_ANALOG: J1.25 (A6), P9.1
/BBC_DIGITAL: J1.6 (D3/INT1), P10.1
/BUZZER: J1.22 (A3), SP1.1
/DIGITAL_SOUND: J1.7 (D4/T0), P14.1
/ECHO: J1.10 (D7/AIN1), U3.3 (ECHO)
/GroveIO1: J1.2 (D0/RX), P12.1
/GroveIO2: J1.1 (D1/TX), P12.2
/LED: J1.8 (D5/T1), R1.2
/LF_L: J1.9 (D6/AIN0), P2.1
/LF_R: J1.21 (A2), P3.1
/SCL: J1.24 (A5), P6.3
/SDA: J1.23 (A4), P6.4
/SERVO: J1.12 (D9/0C1), P16.1
/SWITCH: J1.5 (D2/INT0), R2.2, SW1.1
/TRIG: J1.11 (D8/ICP), U3.2 (TRIG)
GND: C1.2, C2.2, C3.2, D1.1 (K), J1.4 (GND), J1.29 (GND), P1.2, P2.3, P3.3, P6.2, P12.4, P14.3, P15.1, P16.3, SP1.2, SW1.2, U1.4 (GND), U1.5 (GND_1), U1.6 (GND_2), U1.7 (GND_3), U1.14 (GND_4), U1.15 (GND_5), U1.16 (GND_6), U1.17 (GND_7), U2.1 (GND/ADJ), U3.4 (GND), U4.2 (GND)
unnamed: D1.2 (A), R1.1
unnamed: R3.2, U4.5 (RST)
unnamed: R4.2, U4.3 (CH_PD)

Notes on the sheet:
Easy Lab 4 Kids
Power Supply
Arduino Nano
Line Sensor
Motor Driver
ESP-01
BBC Connection
Banana Clip Connector
1xLED
HC-SR04
Piezo Buzzer
MPU-6050 Module
Grove Connector
Sound Sensor
Servo
Push Button

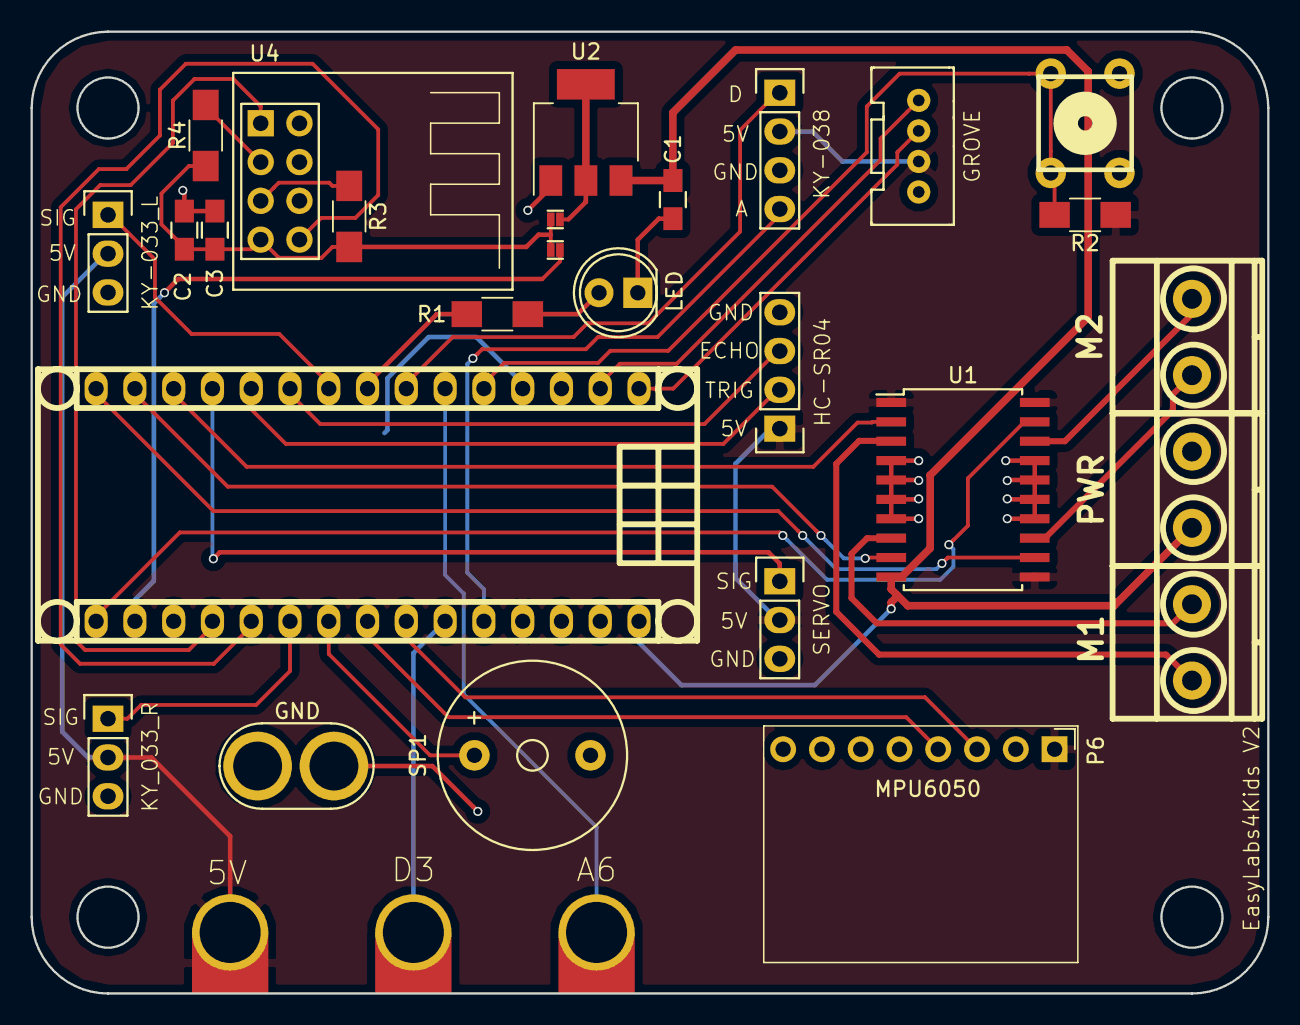
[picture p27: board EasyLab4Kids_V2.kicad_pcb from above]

Board: 2 copper layers, 81.0 x 63.0 mm, 30 parts (0 on the bottom side), 35 nets.

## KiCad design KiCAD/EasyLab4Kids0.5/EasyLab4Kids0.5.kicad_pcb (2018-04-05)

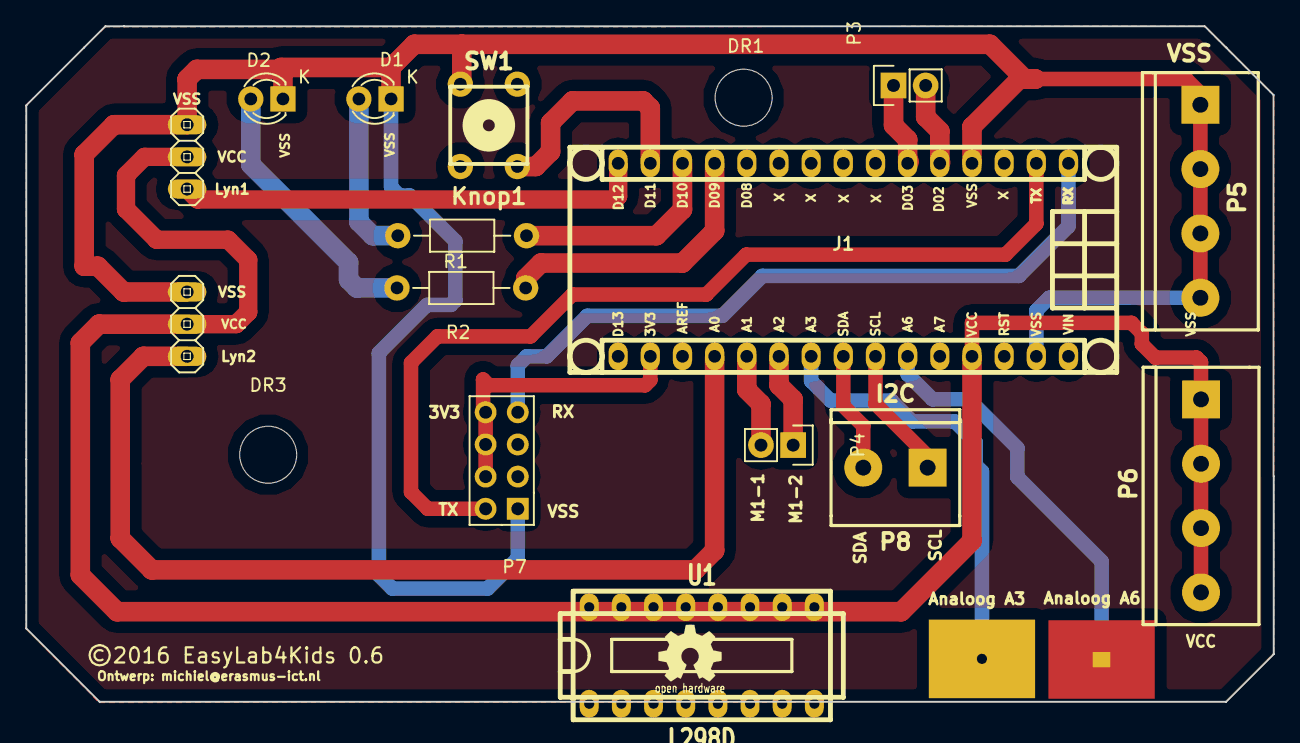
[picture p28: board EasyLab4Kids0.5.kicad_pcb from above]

Board: 2 copper layers, 98.5 x 53.3 mm, 21 parts (1 on the bottom side), 20 nets.

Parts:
D1: LED-G; LED-3MM
D2: LED-R; LED-3MM
DR1: gat1; MountingHole_4.5mm
DR2: CE-LOGO1; Logo_silk_OSHW_6x6mm
DR3: gat2; MountingHole_4.5mm
DR4: Koperplaat A3; EasyPad-8mm
DR5: Logo2; oshw_silkscreen_3
DR6: Koperplaat A6; EasyPad-8mm
J1: Arduino_Nano_Header; arduino_nano_header
P1: KY-033-L; pinhead-1-1X03
P2: KY-033-R; pinhead-1-1X03
P3: MOTOR-R; Pin_Header_Straight_1x02
P4: MOTOR-L; Pin_Header_Straight_1x02
P5: VSS; mors_4p
P6: VCC; mors_4p
P7: ESP8266; ESP-01
P8: I2C; mors_2p
R1, R2: R1k; Resistor_Horizontal_RM10mm
SW1: Knop1; PCB_PUSH
U1: L298D; dil_16-300_socket

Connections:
/3V3: J1.17, P7.4, P7.6, P7.8
/A3: DR4.1, J1.22
/A6: DR6.1, J1.25
/Knop1: J1.14, SW1.2
/LED-G: J1.12, R2.1
/LED-R: J1.13, R1.1
/LYN1: J1.15, P2.1
/LYN2: J1.19, P1.1
/M1-1: J1.20, P4.2, U1.8
/M1-2: J1.21, P4.1, U1.4
/M2-1: J1.6, P3.1
/M2-2: J1.5, P3.2
/SCL: J1.24, P8.1
/SDA: J1.23, P8.2
/VCC: J1.27, P1.2, P2.2, P6.1, P6.2, P6.3, P6.4, U1.5, U1.9
/VSS: D1.1, D2.1, J1.4, J1.29, P1.3, P2.3, P5.1, P5.2, P5.3, P5.4, P7.1, SW1.1, U1.7, U1.11
/Wifi-RX: J1.1, P7.7
/Wifi-TX: J1.2, P7.2
unnamed: D1.2, R1.2
unnamed: D2.2, R2.2

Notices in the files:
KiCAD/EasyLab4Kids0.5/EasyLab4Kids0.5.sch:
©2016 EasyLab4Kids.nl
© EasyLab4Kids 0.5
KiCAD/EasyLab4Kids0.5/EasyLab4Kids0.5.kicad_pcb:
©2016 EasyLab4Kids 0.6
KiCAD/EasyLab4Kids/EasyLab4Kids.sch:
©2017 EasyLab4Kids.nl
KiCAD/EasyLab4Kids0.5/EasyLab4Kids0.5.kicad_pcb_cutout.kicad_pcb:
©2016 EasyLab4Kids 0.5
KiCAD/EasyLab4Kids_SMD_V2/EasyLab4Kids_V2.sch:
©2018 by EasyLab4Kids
